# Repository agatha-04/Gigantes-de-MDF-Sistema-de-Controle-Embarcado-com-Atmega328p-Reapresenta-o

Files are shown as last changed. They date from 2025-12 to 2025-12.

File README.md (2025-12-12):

# Gigantes-de-MDF-Sistema-de-Controle-Embarcado-com-Atmega328p-Reapresenta-o
Firmware, Eletrônica e Documentação Técnica do projeto final da disciplina de Programação de Hardware - 2025.

## Descrição Geral
Esse projeto implementa o sistema eletrônico e programação em C ao robô do projeto final da disciplina Programação de Hardware (2025).
Ele deve:
* Se mover de acordo com os comandos enviados pelo celular via bluetooth (módulo HC-05);
* Controlar os motores por via PWM;
* Detectar impactos do laser inimigo através de um LDR;
* Disparar sua própria arma laser de 1 em 1 segundo;
* Registrar danos (causados pelo laser inimigo) através de LEDs que representam as vidas;
* Reagir ao ser atingido (giro de 180º, perda de uma vida, pausa de 5 segundos);
* Parar o sistema inteiro após a perda das três vidas, reiniciando após apertar o botão de reset.

## Objetivos
* Aplicar conceitos de programação de hardware usando o microcontrolador ATmega328p.
* Projetar um circuito completo de acionamento de motores.
* Implementar controle PWM para movimentação.
* Implementar timers para disparo do laser e rotina de 1 segundo.
* Programar rotinas de interrupção para o botão reset das vidas.
* Criar documentação com o Doxygen.
* Disponilizar todo o código em repositório GitHub.

## Componentes Eletrônicos Usados no Projeto
* 1 microcontrolador do tipo ATmega328p.
* 1 diodo laser de 5V/5mW.
* 1 LDR de 20 milímetros.
* 3 LEDs azuis 10 milímetros.
* 1 CI de ponte H L293d.
* 2 motores DC com faixa de operação de 3V-6V.
* 1 módulo bluetooth HC-05 (para comunicação do controle no celular com o atmega que controla o carrinho).
* Regulador de tensão de 5V (LM7805).
* Regulador de tensão dd 6V (LM7806).
* 2 baterias de 9V.

## Como Testar
- **1.** Gravar o arquivo car_main_final.ino.hex no respectivo microcontrolador.
- **2.** Conectar as baterias ao robô.
- **3.** Testar as respectivas funções:
     * Giro no eixo;
     * PWM dos motores;
     * Disparo do laser:
     * Resposta ao laser inimigo;
     * LEDs de vida;
     * Botão de reset.

## Autores
* **Autor(a):** Agatha Nicole Marques Fávaro - **RA:** 231335
* **Autor(a):** Mykaella Scarllet de Lemos Santana - **RA:** 233508
* **Autor(a):** Rafael Ribeiro de Lima - **RA:** 226326
* Universidade Santa Cecília - Engenharia da Computação
* **Disciplina:** Programação de Hardware - 2/2025
* **Professor(a):** Sérgio Schina de Andrade

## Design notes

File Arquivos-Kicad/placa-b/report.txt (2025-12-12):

Plotted to 'E:\carrinho schina\esquematico-gigante-mdf\placa-b\placa-b-B_Cu.gbr'.
Created Gerber job file 'E:\carrinho schina\esquematico-gigante-mdf\placa-b\placa-b-job.gbrjob'.
Informação: Done.

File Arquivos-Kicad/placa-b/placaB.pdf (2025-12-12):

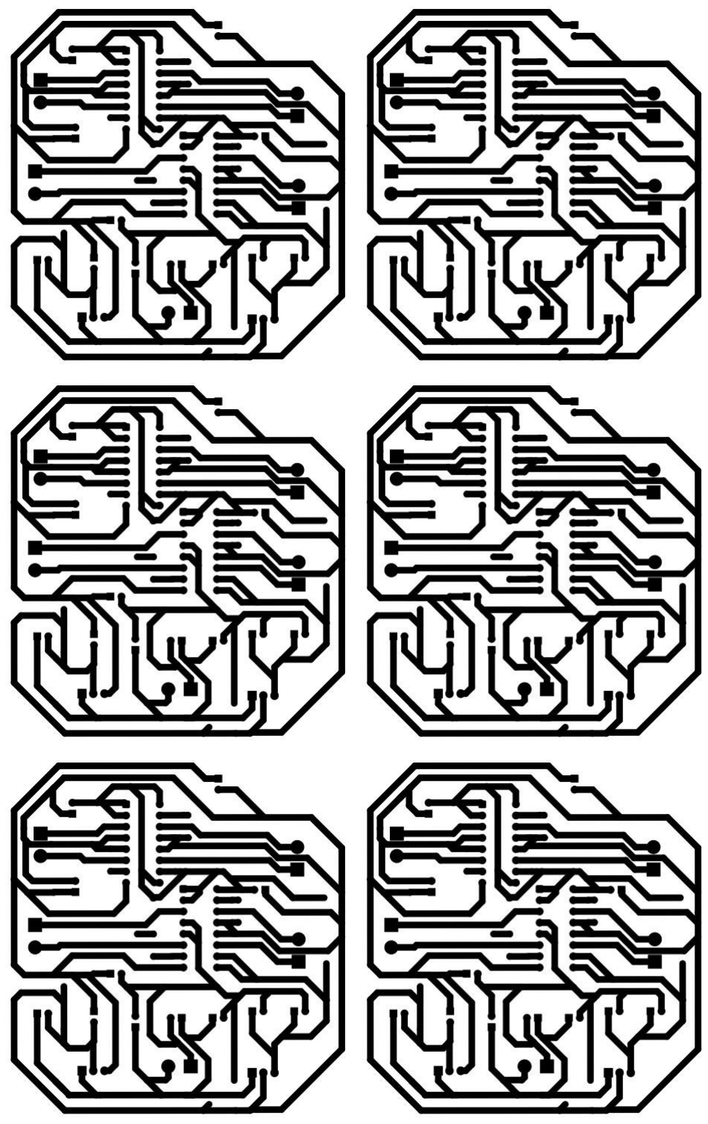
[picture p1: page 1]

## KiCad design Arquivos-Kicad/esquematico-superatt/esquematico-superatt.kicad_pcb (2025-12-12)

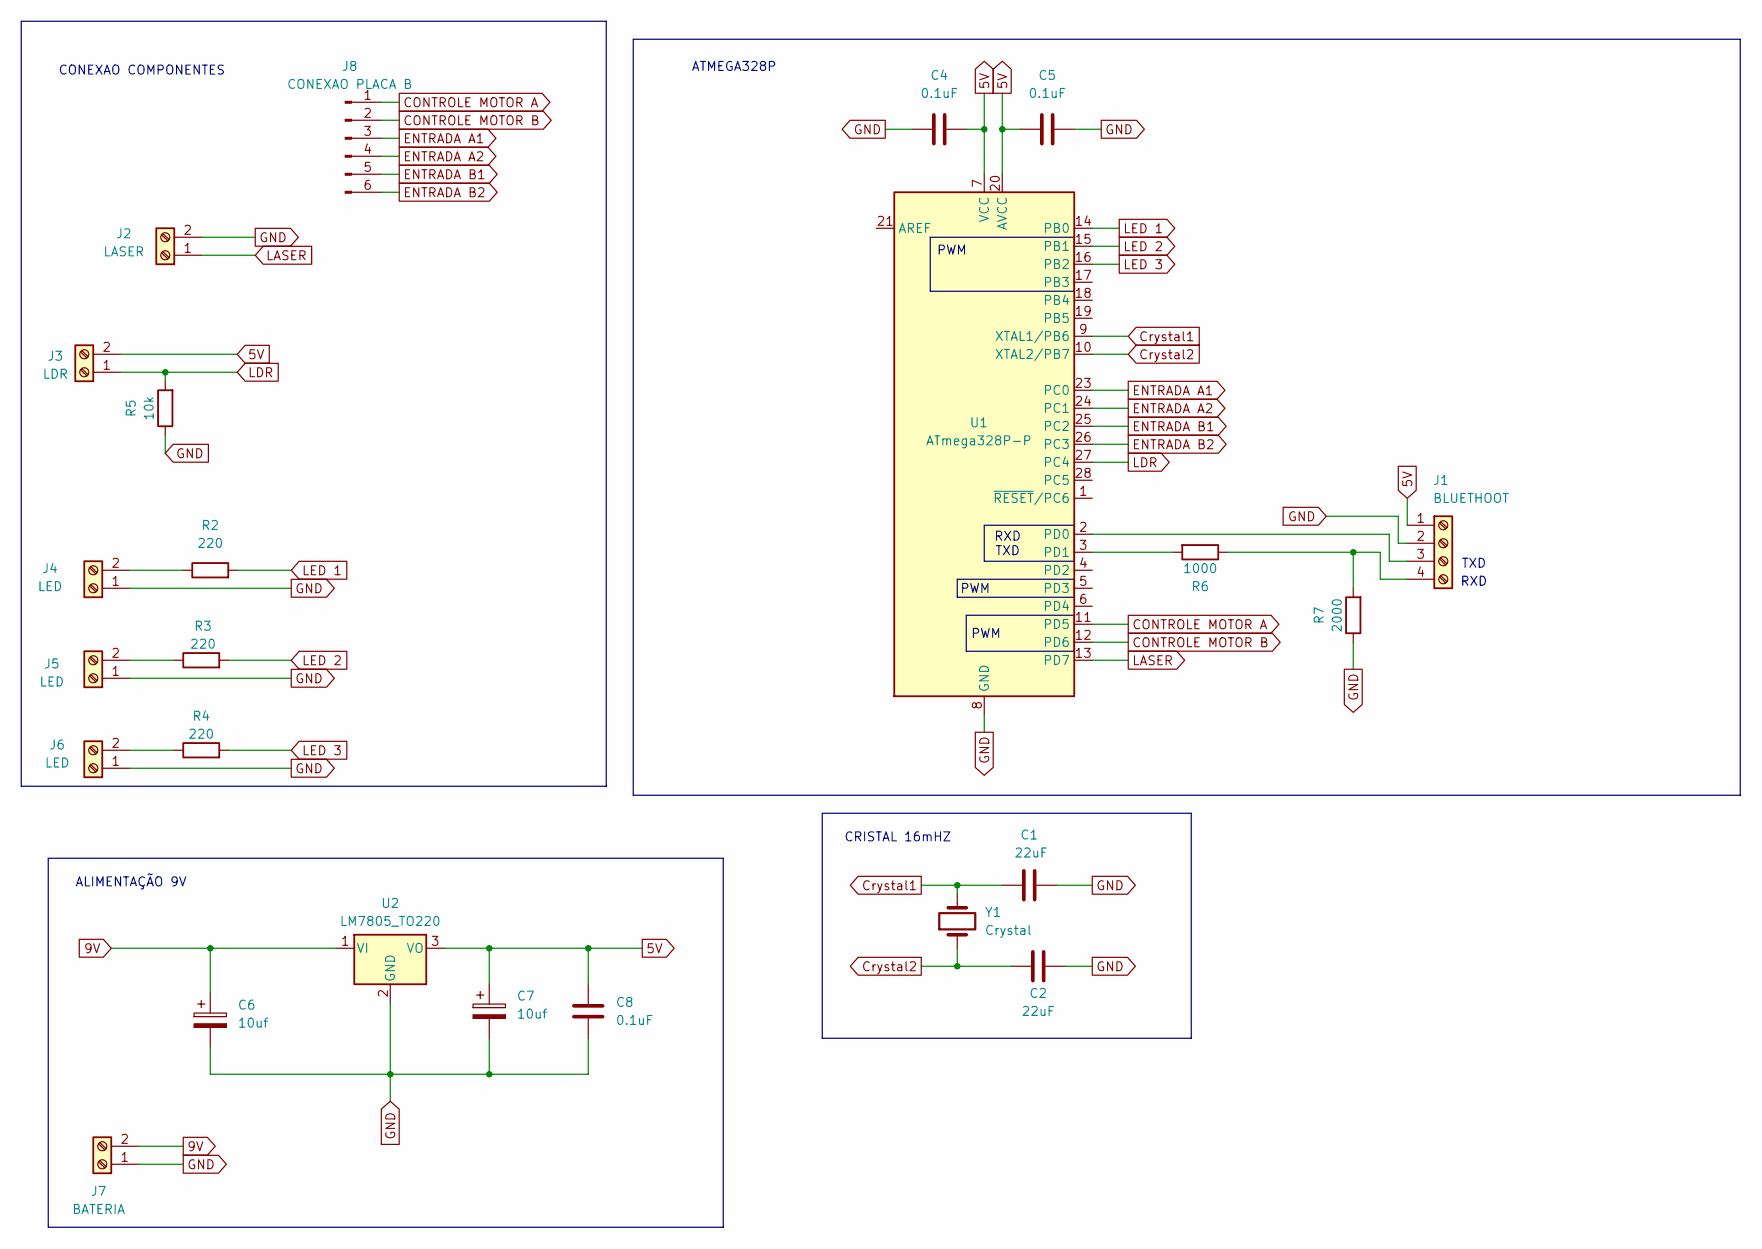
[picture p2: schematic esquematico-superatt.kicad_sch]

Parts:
C1, C2: 22uF; CP_Radial_D7.5mm_P2.50mm
C4, C5, C8: 0.1uF; CP_Radial_D7.5mm_P2.50mm
C6, C7: 10uf; CP_Radial_D7.5mm_P2.50mm
J1: BLUETHOOT; TerminalBlock_bornier-4_P5.08mm
J2: LASER; TerminalBlock_bornier-2_P5.08mm
J3: LDR; TerminalBlock_bornier-2_P5.08mm
J4, J5, J6: LED; TerminalBlock_bornier-2_P5.08mm
J7: BATERIA; TerminalBlock_bornier-2_P5.08mm
J8: CONEXAO PLACA B; PinHeader_1x06_P2.54mm_Vertical
R2, R3, R4: 220; R_Axial_DIN0204_L3.6mm_D1.6mm_P7.62mm_Horizontal
R5: 10k; R_Axial_DIN0204_L3.6mm_D1.6mm_P7.62mm_Horizontal
R6: 1000; R_Axial_DIN0204_L3.6mm_D1.6mm_P7.62mm_Horizontal
R7: 2000; R_Axial_DIN0204_L3.6mm_D1.6mm_P7.62mm_Horizontal
U1: ATmega328P-P; DIP-28_W7.62mm
U2: LM7805_TO220; TO-220-3_Vertical
Y1: Crystal; Crystal_HC49-U_Vertical

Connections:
5V: C4.1, C5.2, C7.1, C8.2, J1.1, J3.2, U1.7 (VCC), U1.20 (AVCC), U2.3 (VO)
9V: C6.1, J7.2, U2.1 (VI)
CONTROLE MOTOR A: J8.1, U1.11 (PD5)
CONTROLE MOTOR B: J8.2, U1.12 (PD6)
Crystal1: C1.1, U1.9 (XTAL1/PB6), Y1.2
Crystal2: C2.1, U1.10 (XTAL2/PB7), Y1.1
ENTRADA A1: J8.3, U1.23 (PC0)
ENTRADA A2: J8.4, U1.24 (PC1)
ENTRADA B1: J8.5, U1.25 (PC2)
ENTRADA B2: J8.6, U1.26 (PC3)
GND: C1.2, C2.2, C4.2, C5.1, C6.2, C7.2, C8.1, J1.2, J2.2, J4.1, J5.1, J6.1, J7.1, R5.1, R7.1, U1.8 (GND), U1.22 (GND), U2.2 (GND)
LASER: J2.1, U1.13 (PD7)
LDR: J3.1, R5.2, U1.27 (PC4)
LED 1: R2.2, U1.14 (PB0)
LED 2: R3.2, U1.15 (PB1)
LED 3: R4.2, U1.16 (PB2)
unnamed: J1.3, U1.2 (PD0)
unnamed: J1.4, R6.1, R7.2
unnamed: J4.2, R2.1
unnamed: J5.2, R3.1
unnamed: J6.2, R4.1
unnamed: R6.2, U1.3 (PD1)

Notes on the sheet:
TXD
PWM
ALIMENTAÇÃO 9V
RXD
ATMEGA328P
CONEXAO COMPONENTES
RXD TXD
CRISTAL 16mHZ

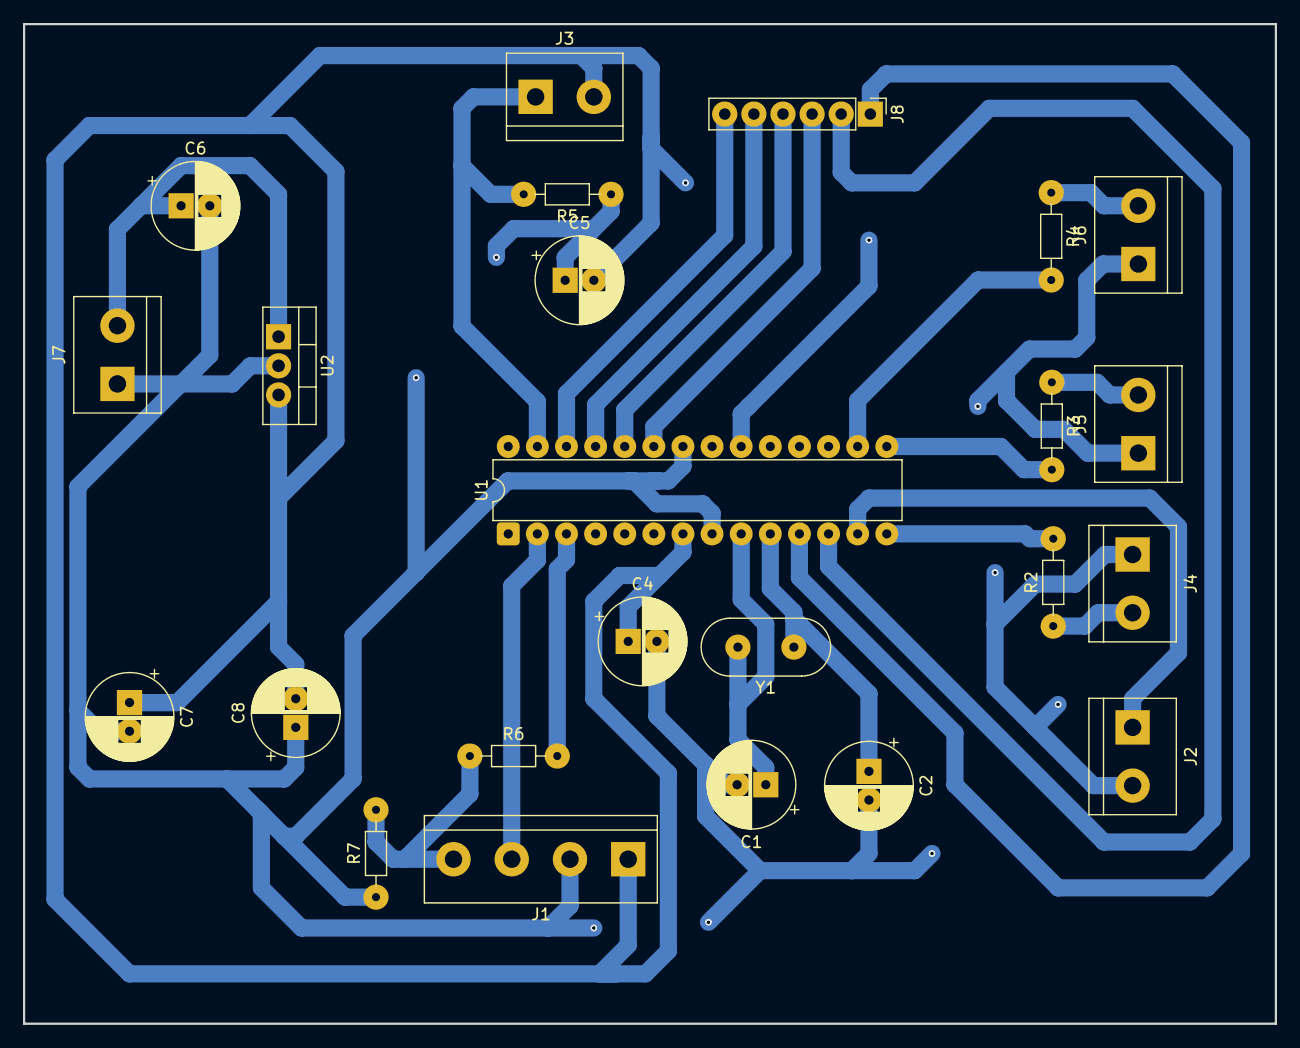
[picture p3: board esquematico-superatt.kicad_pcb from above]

Board: 2 copper layers, 109.2 x 87.2 mm, 24 parts (0 on the bottom side), 22 nets.

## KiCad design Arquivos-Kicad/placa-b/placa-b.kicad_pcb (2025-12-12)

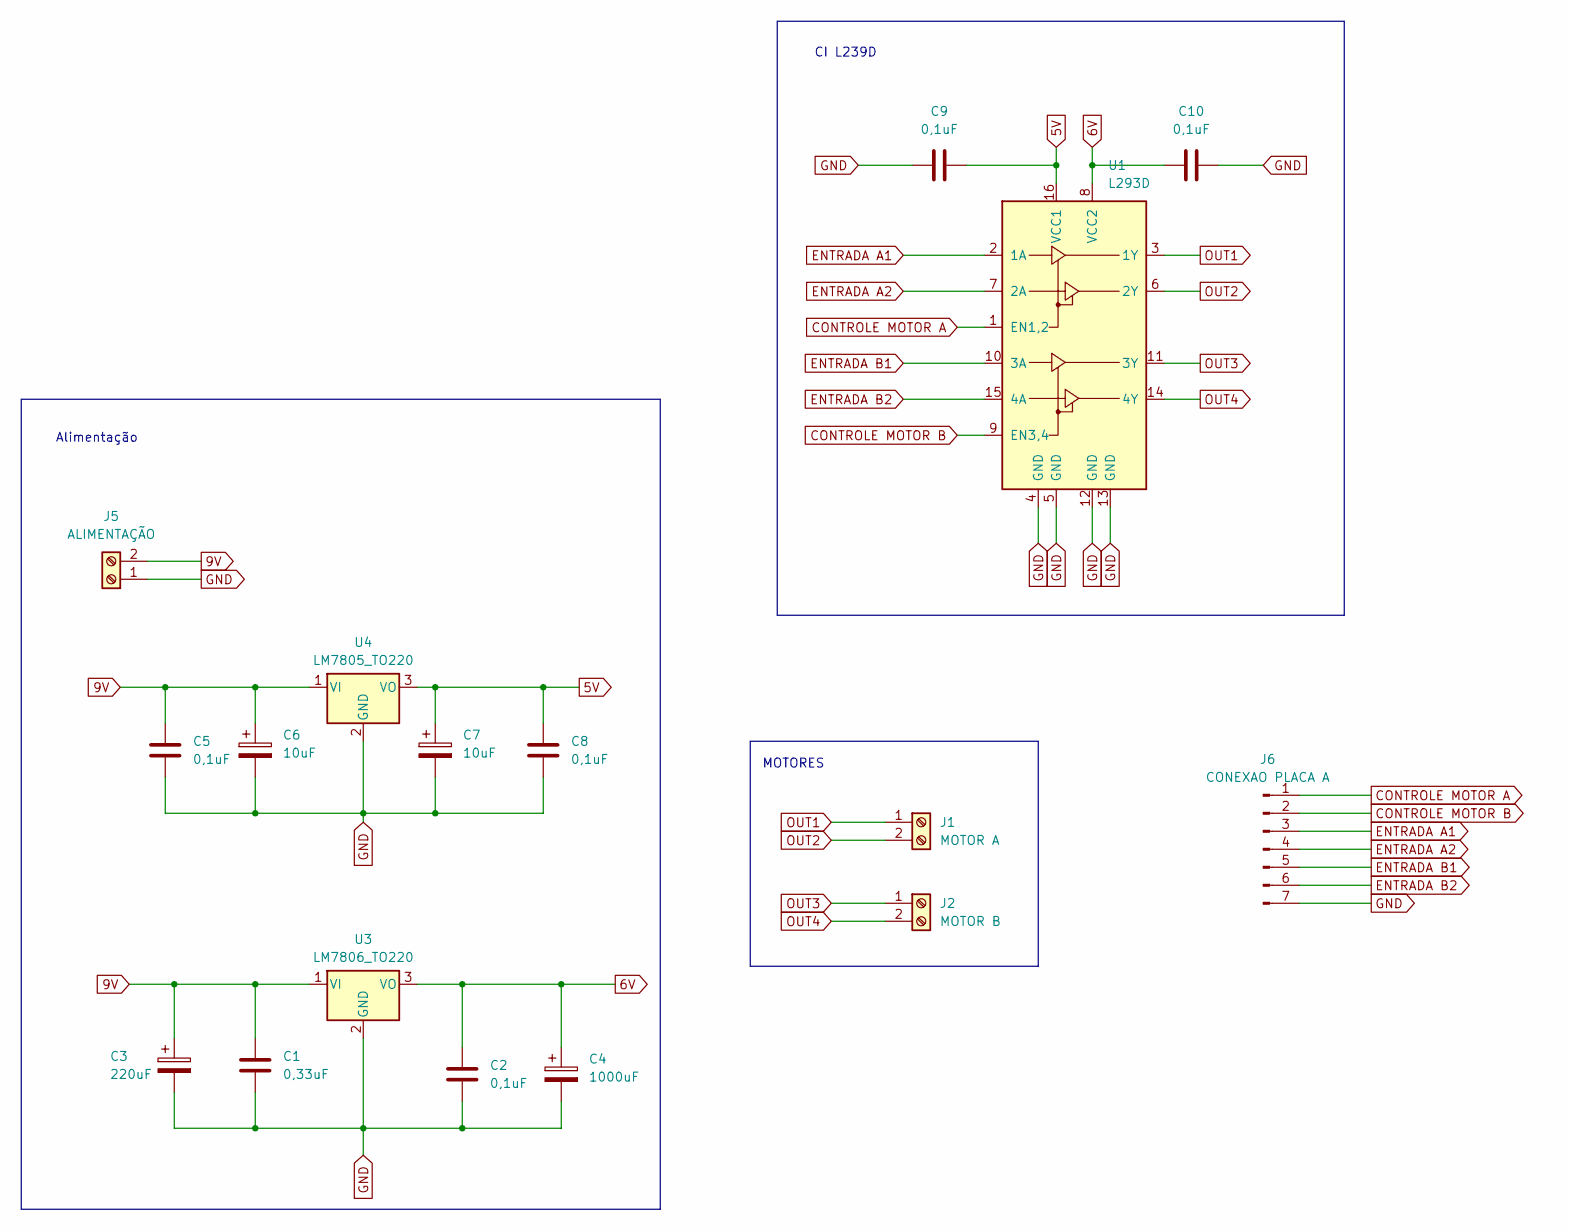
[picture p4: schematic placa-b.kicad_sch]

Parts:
C1: 0,33uF; CP_Radial_D7.5mm_P2.50mm
C2, C5, C8, C9, C10: 0,1uF; CP_Radial_D7.5mm_P2.50mm
C3: 220uF; CP_Radial_D7.5mm_P2.50mm
C4: 1000uF; CP_Radial_D7.5mm_P2.50mm
C6, C7: 10uF; CP_Radial_D7.5mm_P2.50mm
J1: MOTOR A; TerminalBlock_bornier-2_P5.08mm
J2: MOTOR B; TerminalBlock_bornier-2_P5.08mm
J5: ALIMENTAÇÃO; TerminalBlock_bornier-2_P5.08mm
J6: CONEXAO PLACA A; PinHeader_1x07_P2.54mm_Vertical
U1: L293D; DIP-16_W7.62mm
U3: LM7806_TO220; TO-220-3_Vertical
U4: LM7805_TO220; TO-220-3_Vertical

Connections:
5V: C7.1, C8.1, C9.2, U1.16 (VCC1), U4.3 (VO)
6V: C2.1, C4.1, C10.1, U1.8 (VCC2), U3.3 (VO)
9V: C1.1, C3.1, C5.1, C6.1, J5.2, U3.1 (VI), U4.1 (VI)
CONTROLE MOTOR A: J6.1, U1.1 (EN1,2)
CONTROLE MOTOR B: J6.2, U1.9 (EN3,4)
ENTRADA A1: J6.3, U1.2 (1A)
ENTRADA A2: J6.4, U1.7 (2A)
ENTRADA B1: J6.5, U1.10 (3A)
ENTRADA B2: J6.6, U1.15 (4A)
GND: C1.2, C2.2, C3.2, C4.2, C5.2, C6.2, C7.2, C8.2, C9.1, C10.2, J5.1, J6.7, U1.4 (GND), U1.5 (GND), U1.12 (GND), U1.13 (GND), U3.2 (GND), U4.2 (GND)
OUT1: J1.1, U1.3 (1Y)
OUT2: J1.2, U1.6 (2Y)
OUT3: J2.1, U1.11 (3Y)
OUT4: J2.2, U1.14 (4Y)

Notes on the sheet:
MOTORES
Alimentação
CI L239D

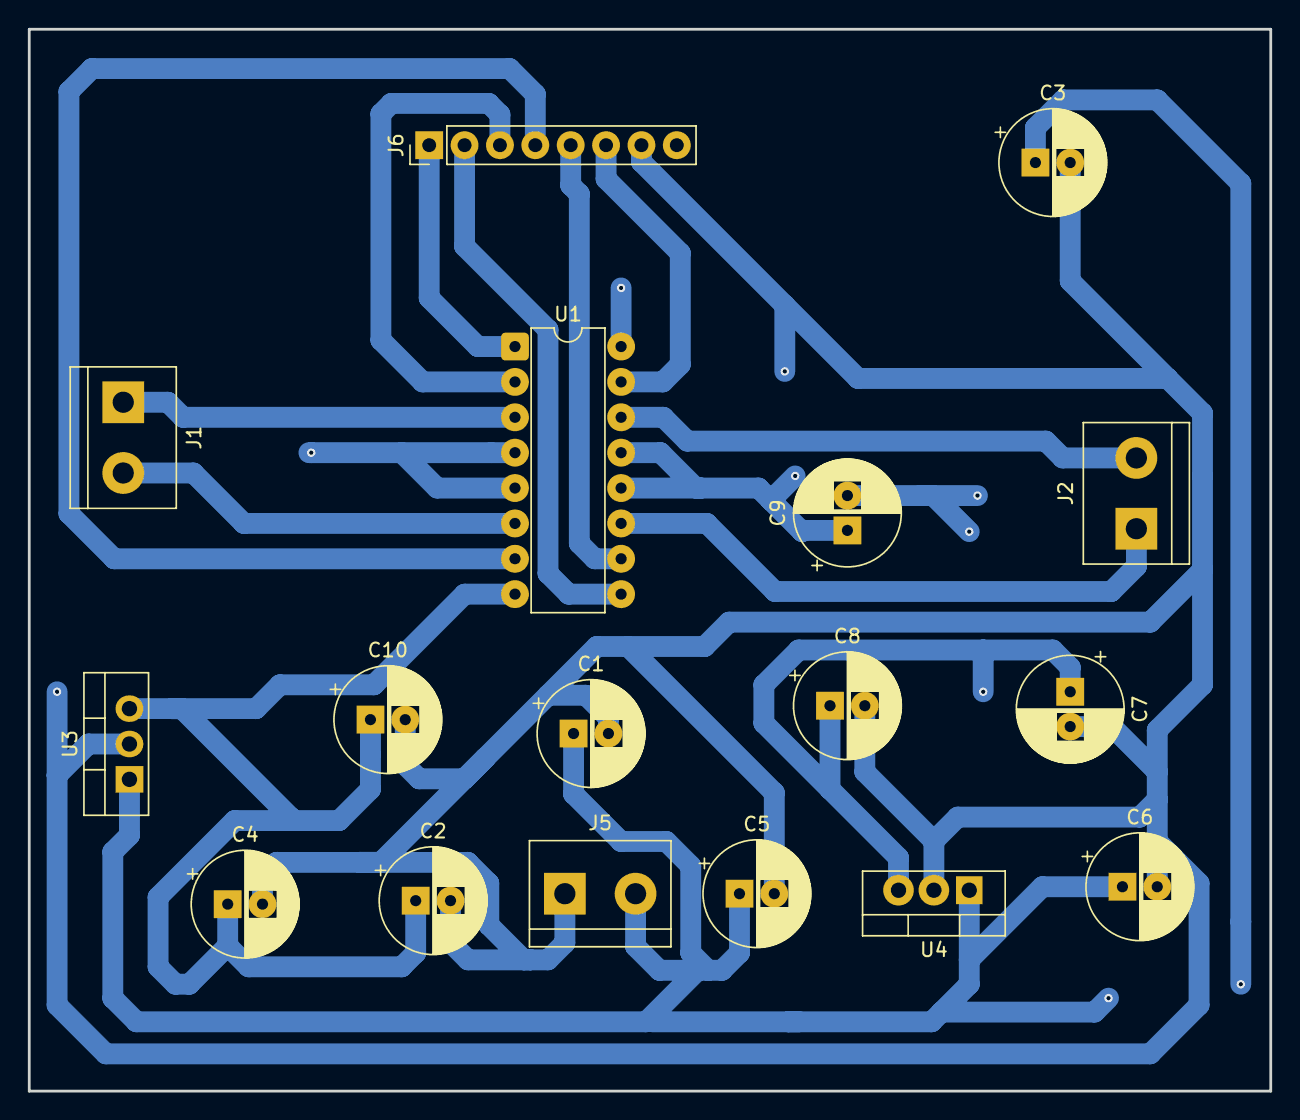
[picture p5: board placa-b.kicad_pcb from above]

Board: 2 copper layers, 89.2 x 76.2 mm, 17 parts (0 on the bottom side), 14 nets.

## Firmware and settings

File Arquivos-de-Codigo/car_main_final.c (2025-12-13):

/*
  car_main_final.c
  ATmega328P, F_CPU = 16MHz
  Integra PWM (OC0A/OC0B) para EN pins, ADC LDR, HC-05 serial, e lógica de "vidas".
  Pinagem:
  - LEDs: PB0, PB1, PB2
  - Laser: PD7
  - LDR: ADC4 (A4)
  - L293D:
      Enable1/2 -> PD5 (OC0B)
      Enable3/4 -> PD6 (OC0A)
      1A -> PC0
      2A -> PC1
      3A -> PC2
      4A -> PC3
  - HC-05:
      TX (HC-05) -> PD0 (RXD)
      RX (HC-05) -> PD1 (TXD)
*/
 
#define F_CPU 16000000UL
#include <avr/io.h>
#include <avr/interrupt.h>
#include <util/delay.h>
#include <stdint.h>
#include <stdbool.h>
 
/* ---------- CONFIGURÁVEIS ---------- */
#define ADC_THRESHOLD 950           // ajuste: valor ADC (0-1023) que conta como "luz forte"
#define DEBOUNCE_MS 50              // tempo de debounce da leitura do LDR
#define LASER_BLINK_INTERVAL_MS 1000UL
#define ROTATE_TIME_MS 700UL        // tempo aproximado para girar ~180° (ajuste conforme seu chassi)
#define PAUSE_AFTER_ROTATE_MS 5000UL // 5 segundos parado
/* ----------------------------------- */
 
/* Pinos (macros) */
#define LED_PORT PORTB
#define LED_DDR  DDRB
#define LED_PIN0 PB0
#define LED_PIN1 PB1
#define LED_PIN2 PB2
 
#define LASER_PORT PORTD
#define LASER_DDR  DDRD
#define LASER_PIN PD7
 
/* Motor control on PORTC */
#define MOT_PORT PORTC
#define MOT_DDR  DDRC
#define M1_IN1 PC0
#define M1_IN2 PC1
#define M2_IN1 PC2
#define M2_IN2 PC3
 
/* Enables on PD5 PD6 (OC0B, OC0A) */
#define ENABLE_PORT PORTD
#define ENABLE_DDR  DDRD
#define EN12 PD5  // OC0B
#define EN34 PD6  // OC0A
 
/* USART baud */
#define BAUD 9600
#define UBRR_VAL ((F_CPU/16/BAUD)-1)
 
/* estado */
volatile uint32_t millis_count = 0; // incrementado por timer0 overflow ~1ms
uint8_t lives = 3;
bool system_locked = false; // true quando vidas = 0 (aguarda reset)
bool reaction_active = false;
 
/* helper: devolve ms */
uint32_t millis(void) {
    uint32_t m;
    uint8_t sreg = SREG;
    cli();
    m = millis_count;
    SREG = sreg;
    return m;
}
 
/* Timer0 overflow ISR: cria um incrementador de ms aproximado */
ISR(TIMER0_OVF_vect) {
    // Timer0 em Fast PWM 8-bit -> overflow ~1.024 ms com prescaler 64
    // contabilizamos cada overflow como 1 ms (pequena imprecisão aceitável)
    static uint8_t accum = 0;
    (void)accum;
    millis_count++;
}
 
/* Inicializa Timer0 para PWM e contagem (Fast PWM, prescaler 64).
   Configura também OC0A/OC0B para saída PWM. */
void timer0_pwm_millis_init(void) {
    // PD6 = OC0A, PD5 = OC0B -> definir como outputs
    DDRD |= (1<<EN12) | (1<<EN34);
 
   
    TCCR0A = (1<<WGM01) | (1<<WGM00) | (1<<COM0A1) | (1<<COM0B1);
    // Prescaler 64
    TCCR0B = (1<<CS01) | (1<<CS00);
 
    
    TIMSK0 |= (1<<TOIE0);
 
    // Inicialmente zero duty
    OCR0A = 0;
    OCR0B = 0;
}
 
/* Ajusta PWM (0..255) para ambas enables */
void motors_pwm(uint8_t val) {
    OCR0A = val; // PD6 -> EN34
    OCR0B = val; // PD5 -> EN12
}
 
/* Inicializa USART (9600, 8N1) */
void usart_init(void) {
    UBRR0H = (uint8_t)(UBRR_VAL >> 8);
    UBRR0L = (uint8_t)(UBRR_VAL & 0xFF);
    UCSR0A = 0;
    UCSR0B = (1<<RXEN0) | (1<<TXEN0); // enable RX/TX
    UCSR0C = (1<<UCSZ01) | (1<<UCSZ00); // 8-bit
}
 
/* enviar um byte */
void uart_send(uint8_t b) {
    while (!(UCSR0A & (1<<UDRE0)));
    UDR0 = b;
}
 
/* checar se há dado disponível e ler (retorna -1 se nada) */
int uart_read_nonblocking(void) {
    if (UCSR0A & (1<<RXC0)) {
        return UDR0;
    }
    return -1;
}
 
/* ADC init e leitura */
void adc_init(void) {
    // AVcc ref, ADC prescaler 128 (125 kHz), ADC enable
    ADMUX = (1<<REFS0); // AVcc como reference, ADC0
    ADCSRA = (1<<ADEN) | (1<<ADPS2)|(1<<ADPS1)|(1<<ADPS0);
}
 
/* Read ADC channel (0..7) */
uint16_t adc_read(uint8_t ch) {
    ch &= 0x07;
    ADMUX = (ADMUX & 0xF8) | ch;
    _delay_us(5);
    ADCSRA |= (1<<ADSC);
    while (ADCSRA & (1<<ADSC));
    return ADC;
}
 
/* Funções motor - usando PWM em enables (OC0A/OC0B) e entradas em PORTC */
void motors_stop(void) {
    // coloca entradas em 0 e duty 0
    MOT_PORT &= ~((1<<M1_IN1)|(1<<M1_IN2)|(1<<M2_IN1)|(1<<M2_IN2));
    motors_pwm(0);
}
 
void motors_forward(void) {
    MOT_PORT |= (1<<M1_IN1) | (1<<M2_IN1);
    MOT_PORT &= ~((1<<M1_IN2) | (1<<M2_IN2));
    motors_pwm(255);
}
 
void motors_back(void) {
    MOT_PORT |= (1<<M1_IN2) | (1<<M2_IN2);
    MOT_PORT &= ~((1<<M1_IN1) | (1<<M2_IN1));
    motors_pwm(255);
}
 
void motors_turn_left(void) {
    MOT_PORT |= (1<<M1_IN2) | (1<<M2_IN1);
    MOT_PORT &= ~((1<<M1_IN1) | (1<<M2_IN2));
    motors_pwm(255);
}
 
void motors_turn_right(void) {
    MOT_PORT |= (1<<M1_IN1) | (1<<M2_IN2);
    MOT_PORT &= ~((1<<M1_IN2) | (1<<M2_IN1));
    motors_pwm(255);
}
 
/* LED */
void leds_all_on(void) {
    LED_PORT |= (1<<LED_PIN0) | (1<<LED_PIN1) | (1<<LED_PIN2);
}
void led_off_index(uint8_t idx) {
    // idx 0 -> PB0, 1 -> PB1, 2 -> PB2
    if (idx == 0) LED_PORT &= ~(1<<LED_PIN0);
    else if (idx == 1) LED_PORT &= ~(1<<LED_PIN1);
    else if (idx == 2) LED_PORT &= ~(1<<LED_PIN2);
}
 
// rotate 180: gira por ROTATE_TIME_MS (time-based)
   
void rotate_180_and_back(void) {
    // gira 180 
 
    // rotate
    MOT_PORT |=  (1<<M1_IN1);
    MOT_PORT &= ~((1<<M1_IN2) | (1<<M2_IN1));
    MOT_PORT |=  (1<<M2_IN2);
    motors_pwm(255);
 
    uint32_t t0 = millis();
    while (millis() - t0 < ROTATE_TIME_MS) { /* aguarda */ }
 
    motors_stop();
 
    // pausa
    t0 = millis();
    while (millis() - t0 < PAUSE_AFTER_ROTATE_MS) { /* aguarda */ }
 
    // volta (inverte)
    MOT_PORT |=  (1<<M1_IN2);
    MOT_PORT &= ~((1<<M1_IN1) | (1<<M2_IN2));
    MOT_PORT |=  (1<<M2_IN1);
    motors_pwm(255);
 
    t0 = millis();
    while (millis() - t0 < ROTATE_TIME_MS) { /* aguarda */ }
 
    motors_stop();
}
 
/* Função que realiza reação ao LDR ser atingido uma vez:
   - apaga 1 LED
   - desliga laser (por segurança)
   - faz sequência de girar 180, pausar 5s, voltar 180
*/
void do_reaction_once(void) {
    if (lives == 0) return;
    reaction_active = true;
 
    // Apaga um LED: usa ordem PB0 -> PB1 -> PB2
    uint8_t idx_to_turn_off = 3 - lives; // se lives=3 -> idx=0; lives=2 -> idx=1; lives=1 -> idx=2
    led_off_index(idx_to_turn_off);
 
    // Laser off (manter desligado durante reação)
    LASER_PORT &= ~(1<<LASER_PIN);
 
    // Sequência: girar 180, pausar, voltar
    rotate_180_and_back();
 
    // decrementa vidas
    if (lives > 0) lives--;
    if (lives == 0) {
        system_locked = true;
        motors_stop();
        // laser já desligado
    } else {
        // após reação, laser voltará a piscar no loop principal
    }
 
    reaction_active = false;
}
 
/* Processa comando recebido por bluetooth */
void process_command(char c) {
    if (reaction_active) return; // ignorar comandos durante reação
    if (system_locked) {
        if (c == 'X' || c == 'x') {
            // reset system
            lives = 3;
            leds_all_on();
            system_locked = false;
            // laser pode voltar a piscar
        }
        return;
    }
 
    switch (c) {
        case 'F': case 'f': motors_forward(); break;
        case 'B': case 'b': motors_back(); break;
        case 'L': case 'l': motors_turn_left(); break;
        case 'R': case 'r': motors_turn_right(); break;
        case 'S': case 's': motors_stop(); break;
        case 'X': case 'x': // reset from BT
            lives = 3;
            leds_all_on();
            system_locked = false;
            break;
        default:
            // ignorar
            break;
    }
}
 
/* main */
int main(void) {
    /* portas */
    LED_DDR |= (1<<LED_PIN0)|(1<<LED_PIN1)|(1<<LED_PIN2);
    // começa LEDs off; depois ligamos
    LED_PORT &= ~((1<<LED_PIN0)|(1<<LED_PIN1)|(1<<LED_PIN2));
 
    LASER_DDR |= (1<<LASER_PIN);
    LASER_PORT &= ~(1<<LASER_PIN);
 
    // motor input pins on PORTC
    MOT_DDR |= (1<<M1_IN1)|(1<<M1_IN2)|(1<<M2_IN1)|(1<<M2_IN2);
 
    // initialize motors outputs low
    MOT_PORT &= ~((1<<M1_IN1)|(1<<M1_IN2)|(1<<M2_IN1)|(1<<M2_IN2));
 
    // Inicializa ADC, USART, Timer0 (PWM+millis)
    adc_init();
    usart_init();
    timer0_pwm_millis_init();
 
    sei(); // enable interrupts
 
    // estado inicial
    leds_all_on();
    system_locked = false;
    lives = 3;
 
    uint32_t last_laser_toggle = millis();
    bool laser_state = true;
    LASER_PORT |= (1<<LASER_PIN); // laser ligado inicialmente
    last_laser_toggle = millis();
 
    uint32_t last_ldr_sample = 0;
    const uint16_t threshold = ADC_THRESHOLD;
 
    for (;;) {
        // 1) piscar laser (quando sistema não bloqueado e não em reação)
        if (!system_locked && !reaction_active) {
            uint32_t now = millis();
            if (now - last_laser_toggle >= LASER_BLINK_INTERVAL_MS) {
                laser_state = !laser_state;
                if (laser_state) LASER_PORT |= (1<<LASER_PIN);
                else LASER_PORT &= ~(1<<LASER_PIN);
                last_laser_toggle = now;
            }
        } else {
            // se sistema bloqueado ou em reação, manter laser desligado
            LASER_PORT &= ~(1<<LASER_PIN);
        }
 
        // 2) ler UART não-bloqueante
        int r = uart_read_nonblocking();
        if (r >= 0) {
            process_command((char)r);
        }
 
        // 3) LDR sampling (não enquanto bloqueado)
        if (!system_locked && !reaction_active) {
            uint32_t now = millis();
            if (now - last_ldr_sample >= DEBOUNCE_MS) {
                last_ldr_sample = now;
                // ADC4 = channel 4
                uint16_t val = adc_read(4);
                if (val >= threshold) {
                    // luz forte detectada -> reação
                    do_reaction_once();
                }
            }
        }
 
        // loop leve
    }
 
    return 0;
}
 

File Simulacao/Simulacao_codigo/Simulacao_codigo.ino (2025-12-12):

#define F_CPU 16000000UL
#include <avr/io.h>
#include <util/delay.h>

// ====== DEFINIÇÕES ======
#define LDR_CHANNEL 4      // ADC4 = A4
#define BUTTON_PIN  PD4
#define LASER_PIN   PD7

#define LED1 PB0
#define LED2 PB1
#define LED3 PB2

// Motores L293D
#define EN12 PD5
#define EN34 PD6
#define M1A PC0
#define M1B PC1
#define M2A PC2
#define M2B PC3

// ====== VARIÁVEIS ======
uint8_t vidas = 3;
uint8_t laser_state = 0;

// ===============================
//       Leitura do ADC (LDR)
// ===============================
uint16_t read_adc(uint8_t ch)
{
    ADMUX = (1 << REFS0) | (ch & 0x07);   // AVcc + canal
    ADCSRA |= (1 << ADSC);               // inicia conversão
    while (ADCSRA & (1 << ADSC));        // espera terminar
    return ADC;
}

// ===============================
//     Controle do Laser (pisca)
// ===============================
void laser_blink()
{
    laser_state ^= 1;
    if (laser_state)
        PORTD |= (1 << LASER_PIN);
    else
        PORTD &= ~(1 << LASER_PIN);
}

// ===============================
//       Controle dos motores
// ===============================
void motores_parar() {
    PORTD &= ~((1 << EN12) | (1 << EN34));
}

void motores_frente() {
    PORTC = (1 << M1A) | (1 << M2A);
    PORTD |= (1 << EN12) | (1 << EN34);
}

void motores_direita() {
    PORTC = (1 << M1A) | (1 << M2B);
    PORTD |= (1 << EN12) | (1 << EN34);
}

void motores_esquerda() {
    PORTC = (1 << M1B) | (1 << M2A);
    PORTD |= (1 << EN12) | (1 << EN34);
}

void motores_re() {
    PORTC = (1 << M1B) | (1 << M2B);
    PORTD |= (1 << EN12) | (1 << EN34);
}

void motores_giro180() {
    PORTC = (1 << M1A) | (1 << M2B);
    PORTD |= (1 << EN12) | (1 << EN34);
    _delay_ms(850);   // ajuste fino conforme motor real
    motores_parar();
}

// ===============================
//          MAIN
// ===============================
int main(void)
{
    // LEDs
    DDRB |= (1 << LED1) | (1 << LED2) | (1 << LED3);

    // Laser
    DDRD |= (1 << LASER_PIN);

    // Motores
    DDRD |= (1 << EN12) | (1 << EN34);
    DDRC |= (1 << M1A) | (1 << M1B) | (1 << M2A) | (1 << M2B);

    // Botão PD4
    DDRD &= ~(1 << BUTTON_PIN);
    PORTD |= (1 << BUTTON_PIN); // pull-up

    // ADC config
    ADCSRA = (1 << ADEN) | (1 << ADPS2) | (1 << ADPS1); // Prescaler 64

    // LEDs começam acesos
    PORTB |= (1 << LED1) | (1 << LED2) | (1 << LED3);

    uint16_t ldr;
    uint16_t threshold = 300;   // mais sensível!

    while (1)
    {
        // ========================
        //  Vida acabou → aguarda botão
        // ========================
        if (vidas == 0) 
        {
            motores_parar();
            PORTD &= ~(1 << LASER_PIN);

            while (PIND & (1 << BUTTON_PIN)); // espera reset

            vidas = 3;
            PORTB |= (1 << LED1) | (1 << LED2) | (1 << LED3);
        }

        // Pisca laser a cada 500ms
        laser_blink();

        // Faz o ciclo dos motores com checagem do LDR entre passos
        for (uint8_t etapa = 0; etapa < 4; etapa++)
        {
            if (etapa == 0) motores_frente();
            if (etapa == 1) motores_direita();
            if (etapa == 2) motores_esquerda();
            if (etapa == 3) motores_re();

            // 2s por etapa, dividido em 4 blocos de 500ms
            for (uint8_t i = 0; i < 4; i++)
            {
                // Pisca laser
                laser_blink();

                // Leitura do LDR
                ldr = read_adc(LDR_CHANNEL);

                if (ldr > threshold)
                {
                    vidas--;

                    if (vidas == 2) PORTB &= ~(1 << LED3);
                    else if (vidas == 1) PORTB &= ~(1 << LED2);
                    else if (vidas == 0) PORTB &= ~(1 << LED1);

                    PORTD &= ~(1 << LASER_PIN);

                    motores_giro180();
                    motores_parar();

                    for (uint8_t p = 0; p < 5; p++)
                        _delay_ms(1000);

                    goto continuar_loop;
                }

                _delay_ms(500);
            }
        }

        continuar_loop:
        continue;
    }
}
